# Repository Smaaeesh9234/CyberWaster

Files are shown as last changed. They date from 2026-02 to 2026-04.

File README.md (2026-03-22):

# CyberWaster
Files used for the CyberWaster Project

Place any notes that you have about the cyberwaster here. This should include any hardware and complications

## Lidar System:

$8.00 [Nema 17 Bipolar Stepper Motor](https://www.omc-stepperonline.com/nema-17-bipolar-1-8deg-16ncm-22-6oz-in-1a-3-7v-42x42x20mm-4-wires-17hs08-1004s)

$25.00 [LiDAR sensor](https://www.amazon.com/Wishiot-TF-Luna-Single-Point-Terminal-WiFi_Lora_32/dp/B09PZ559ZB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)

$15.00 (only if doing 360° scan) [Slip ring](https://www.digikey.com/en/products/detail/adafruit-industries-llc/736/5353612)

$7.00 [A4988 Motor Driver](https://www.digikey.com/en/products/detail/adafruit-industries-llc/6109/25897273)

[Arduino Kit Components:](https://www.elegoo.com/blogs/arduino-projects/elegoo-mega-2560-the-most-complete-starter-kit-tutorial)
Arduino Mega

## Motor System

## ROS 2

<tutorial Links here>
https://docs.ros.org/en/humble/Installation.html

## Gazebo

<install and use gazebo links>
https://gazebosim.org/docs/fortress/getstarted/

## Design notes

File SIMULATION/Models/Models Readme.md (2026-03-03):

Place your .stl files here for your models or any other file types. this is for the 3d models specifically

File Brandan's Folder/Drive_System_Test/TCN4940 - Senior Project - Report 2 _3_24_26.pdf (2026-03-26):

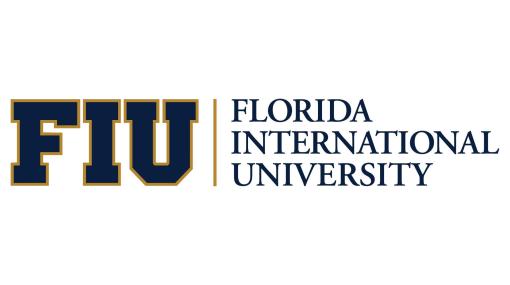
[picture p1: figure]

### Department of Electrical and Computer Engineering

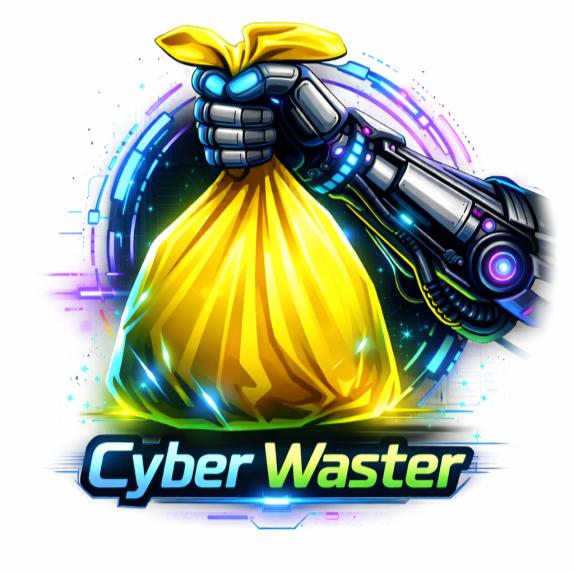
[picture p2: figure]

TCN4940 RVC 1261 - Senior Project Spring 2026

## CyberWaster

### The Waste Handlers

Team Leader: Brandan Gerbers (6448449) Sabrina Ruiz (6338671)
Ellowyn Taylor (6352591)
Samir Zelaya (6474641)
Sebastian Klee (6307554)
Giovanni Nieves (6198045)
Instructor: Gustavo Chaparro Baquero Mentor: Dr. Lauren Ervin

Date: February 2026

## I. SUMMARY AND PROBLEM STATEMENT

Abstract
This project aims to look at how waste collection can be improved by using sensors and automation. Most waste system projects only react to how to solve the problem, instead of using data and trends to make decisions. The current approach is inefficient and labor intensive. We are planning to create a simulated robot environment for testing and use those learnings to create a small-scale prototype that will check the waste level, determine when the bin is full, and navigate to a trash disposal location. This project's primary focus is to create the required technology needed for autonomous navigation and to discover the required sensors for collecting waste level data.

Executive summary

This project approaches waste collection as a logistics and optimization problem by integrating sensing, analytics, and autonomous navigation. The system improves collection efficiency while generating useful insights into waste usage behavior. Designed for scalability, the architecture supports residential, assisted-living, and broader smart infrastructure environments. The system autonomously travels from a designated resting location to a disposal point when waste sensors detect that a bin has reached a predefined fill level. This approach reduces manual effort, improves safety, and demonstrates how automation can enable more efficient and data-informed waste management.

Problem Statement

Current waste collection systems rely on fixed schedules and manual observation rather than real-time data, resulting in inefficient labor usage, increased operational costs, and missed opportunities for optimization. Limited visibility into waste fill levels, weight, and usage patterns prevents waste and recycling services from making informed, data-driven decisions. Routine waste handling presents a physical challenge for individuals with limited mobility, including elderly and physically disabled populations. Tasks such as lifting and transporting waste bins require strength, balance, and repeated effort, which can pose safety risks and reduce independence. As the cost of living continues to rise, inefficiencies in time and labor associated with household waste disposal continue to be a consistent task. These combined challenges highlight the need for a solution that reduces physical effort, improves efficiency, and enables smarter waste management through improved visibility and automation.

## II. NEED SPECIFICATIONS

Objectives | Specification | Justification
1, 6 | An AprilTag signals the robot where to travel. | It automates waste disposal, which would save a person’s time and energy.
2 | LiDAR sensors detect any blocking obstacles in real time and turn accordingly. | It prevents any collisions that could occur and allows the robot to safely navigate in an environment.
3, 4 | An ultrasonic distance sensor alongside 1-4 load cell sensors would measure the levels of waste and signal the robot when it is full. | It ensures that the robot will have accurate detection to correctly decide when traveling is necessary.
5 | The data over time of the waste levels would be analyzed for patterns. | It helps optimize schedules for waste collection and efficiently provides a user’s waste patterns for collectors.

Objectives

1. The robot should be able to carry trash to a designated location.
2. The robot should be able to avoid obstacles in its path.
3. The robot should be able to monitor waste levels.
4. The robot should be able to detect if the trash bin is full.
5. The robot should be able to comprehend data of the user’s waste usage.
6. The robot should be able to reduce the amount of labor for the user.
A. Assumption
⚫ | The QR code sticker is placed correctly at destination points for drop off.
⚫ | Elderly and physically disabled users are willing to allow an assistive robotic system to
| support routine waste handling tasks.
⚫ | Users will not be required to directly interact with the system during normal operation.
⚫ | The LiDAR sensor will detect appropriate sizes of obstacles.
B. Limitation

⚫ | Designed to operate with minimal human feedback
⚫ | Operation is limited to indoor environments and outdoor concrete or similar flat surfaces.
⚫ | The system is not designed to operate on uneven terrain, stairs, or soft ground surfaces
| such as grass or gravel.
⚫ | Performance may be affected by environmental factors such as lighting conditions,
| obstacles, or layout complexity.
C. Operating Environment
Environment Details | Reference Images

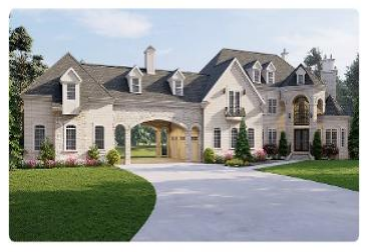
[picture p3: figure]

Residential Single-Family Home
(Large Property)
The system is intended to operate in a residential environment with a paved driveway, landscaped surroundings, and a clearly defined curbside waste collection point. Navigation paths are primarily flat concrete surfaces with minimal elevation changes. Potential obstacles include parked vehicles, outdoor furniture, and pedestrians. Operation is expected to occur in low to moderate traffic conditions.

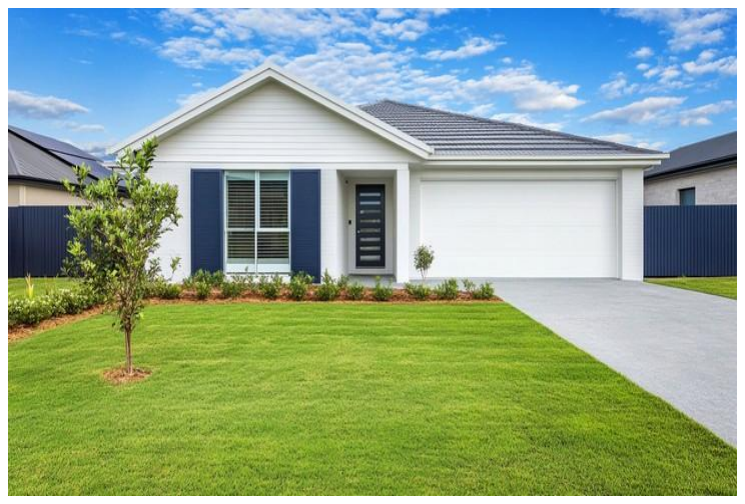
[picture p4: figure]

Residential Single-Family Home (Suburban Property)
This environment represents a typical suburban household with a short driveway and direct access from the home to the curb. The operating surface consists of smooth concrete with grass or landscaping adjacent to travel paths. The system must safely navigate near the home entrance, driveway edges, and curbside collection area while accounting for people, pets, and common household obstacles.

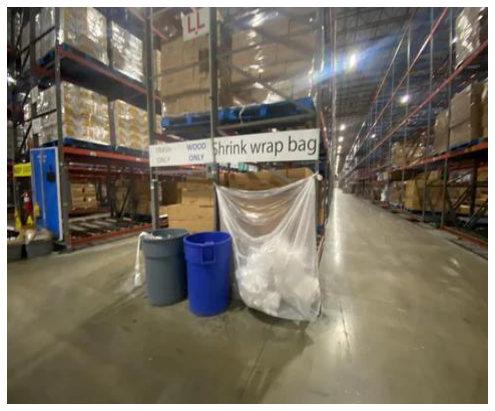
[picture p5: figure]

Indoor Facility / Warehouse-Style Environment This environment represents indoor operational areas such as assisted-living facilities and storage areas. The system operates on polished concrete flooring with defined pathways and frequent human activity. Obstacles may include carts, bins, shelving, and temporary obstructions. Reliable obstacle detection and controlled movement are critical due to shared use of space with staff and occupants.

D. Intended Users and Intended Uses
1. Intended Users:
⚫ | Elderly people (65+)
⚫ | Adults with physical limitations
⚫ | Secondary users such as caregivers and faculty staff
2. Intended Uses:
⚫ | Operates in indoor warehouses or concrete floors.
⚫ | To collect trash and transport it to a drop off location.
⚫ | Reduce labor associated with waste disposal.

## III. NEED ANALYSIS

A. Purpose

The purpose of this project is to address inefficiencies in current waste collection practices by shifting from manual, schedule-based operations to a data-informed, and automated approach. Particular emphasis is placed on supporting populations for whom routine waste handling can be physically challenging, such as elderly and physically disabled individuals. By leveraging sensing, analytics, and autonomous mobility, the project demonstrates how waste monitoring and relocation can be optimized through real-time data and intelligent system behavior.

B. Client Need Statement

The client needs a waste collection system that provides real-time visibility into waste fill levels and usage patterns, reduces dependence on manual observation and fixed schedules, and enables autonomous relocation of waste containers. Smart sensors have helped cities dispatch collection trucks only when needed, reducing unnecessary trips and garbage overflow [1]. The company expressed that it reduced unnecessary collections and garbage overflow. Smart bins can optimize collection schedules by detecting anomalies, such as sudden increases in waste volume [2]. The system should specifically reduce physical effort and safety risks for elderly and physically disabled users while improving overall operational efficiency and decision-making.

C. Data Collection

Needs were identified through:

⚫ | A structured interview with the project mentor acting as the client
⚫ | A survey of potential end users
⚫ | Team brainstorming sessions to uncover additional needs

Mentor-Client Interview

Questions | Answers
On a scale of 1–10, how physically demanding do you find handling waste? | 10
How challenging is this task for you to perform on a regular basis? | Very
How often do you find yourself disposing of waste outside your home? | Once a week
How much assistance would make this task easier for you? | Full autonomy
Would you find analytics about your waste behavior helpful in reducing said waste? | Yes
Is the cost of having waste disposed of something you would like to be reduced? | Yes

Potential End Users Characteristics

Socioeconomics | Age | Primarily elderly adults (65+) and adults with physical limitations; secondary users include caregivers and facility staff.
| Gender | Any
| Income | Expected users would be middle class or higher. This would give an average wage of $56,000+
| Education | Varied educational backgrounds. Systems must be intuitive and not require technical knowledge.
| Disability | Users may have mobility impairments, reduced strength, balance issues, or limited dexterity; the system should minimize physical exertion and risk.
Behavioral | Hobbies | Low to moderate physical activity hobbies. Social hobbies, such as card games with friends and family.
| Reading Interest | General news, lifestyle content, or light informational material. Preference for simple, clear instructions.
| Waste Handling Difficulty | Waste handling may be physically challenging due to weight, bending, balance, or distance to disposal location; users may avoid timely disposal due to effort or safety concerns.
Psychological | Listless | Many expected users would be low energy people, requiring the need for external products to aid in tasks.
| Technology Comfort Level | Varies from low to moderate; the system should feel supportive rather than complex or intimidating.
| Independence | Strong desire to maintain independence and avoid reliance on caregivers.

Team Brainstorming Notes

Identified Challenge | Potential Approach or Consideration
Difficulty moving heavy waste bins | Reduce or eliminate the need for manual bin transport
Risk of falls during waste disposal | Minimize physical handling and walking distance required
Reliance on staff for waste relocation | Enable automated or assisted waste movement
Manual checking of bin fill levels | Provide automated indication of waste capacity status
Desire for resident independence | Support hands-off operation with minimal user interaction
Traffic and obstacle avoidance | High potential of running into people or objects during transit
High potential for missing trash pickup time | A system that is able to transfer waste at a scheduled time or based on environmental condition.
D. Identified Attributes

Main Objective

⚫ Demonstrate relocation systems using simulation and/or a small-scale physical prototype.
⚫ Implement accurate waste capacity sensing to measure bin fill levels.
⚫ Create a simulated environment to demonstrate autonomous robot behavior, system logic, and data flow.
⚫ Collect data to understand the waste usage patterns
⚫ Stay within the project budget

Secondary Objectives

⚫ Define and document a scalable system architecture suitable for expansion to larger environments.
⚫ Design and implement a small-scale physical prototype to validate real-world feasibility.
⚫ Trigger collection and relocation behavior based on predefined waste thresholds. ⚫ Checking the bin weight to prevent overloading the robot with waste

⚫ Limit the movement of the robot if the load is too heavy

Constraints

⚫ Total prototype system cost shall not exceed $800
⚫ Robot shall safely carry a minimum payload of 5 pounds
⚫ Robot shall autonomously navigate to a designated location 15 feet away with a positional accuracy of ±1 foot
⚫ System shall operate reliably on cement flooring and be able to have obstacle detection
⚫ Power system shall support at least two complete autonomous relocation cycle per charge
E. Grouped Objectives

The remaining objectives were grouped into parent categories to clarify design priorities.

Safety

⚫ | The system should operate without posing risk to users
⚫ | The system should operate without posing risk to pets or local wildlife
⚫ | All electrical and battery parts should be protected to prevent any shocks or fire from
| happening.

Usability

⚫ | The system should be easy to operate and understand
⚫ | Optional commands to enhance the user experience and improve the product as the
| user becomes familiar with it
⚫ | The system should provide some feedback to the user about the waste level.

Reliability

⚫ | The system should function consistently with minimal intervention
⚫ | The system should move smoothly and avoid any obstacles in its path.
⚫ | The system should be able to handle different terrains without getting stuck.
F. Resulting Problem Statement

This project aims to design an autonomous waste monitoring and relocation system that addresses inefficiencies in manual waste handling while improving safety, usability, and reliability. The system should reduce physical effort and safety risks for users with limited mobility, support independent operation, and provide consistent, data-informed waste handling behavior in residential and assisted-living environments.

The objectives identified through this need specific and analysis provide the foundation for defining the specifications and requirements to ensure the project solves a real-world problem.

## IV. FEASIBILITY AND RISK ANALYSIS

A. Technical Feasibility

CyberWaster relies on established robotics, such as the load cells, LiDAR sensors, or the AprilTags. These components are available and can be obtained locally or through online purchases. The system will be using already established frameworks like ROS 2 and Gazebo for simulation. This project relies on existing technologies, making the overall technical risk moderate but manageable.

Below is an assessment conducted by the team ranking the feasibility of set attributes. 5 is a highly feasible option, and 1 is a low-chance feasibility.

Attribute | Score | Why | Solution
Does the technology exist? | 5 | Yes. | Using existing components like LiDAR sensors, wheels, Gazebo simulation, etc.
Is it available locally or online? | 5 | Yes, both. | All components are distributed in stores and online stores like Amazon. Some members possess a 3D printer, and FIU has several as well.
Can it be obtained? | 4 | Yes, however, we require finance. | Our team set price targets for hardware, funding the project ourselves by using open-source software packages.
Are fundamentally new inventions required? | 4 | Just the 3D structure of CyberWaster. | Design and print the 3D structure of CyberWaster.
How much Technical Risk is there? | 3 | Ensuring functionality of the hardware and software can be difficult. | Completely build CyberWaster and test its function in different layouts with the simulation.
Total | 21
Average | 4.2

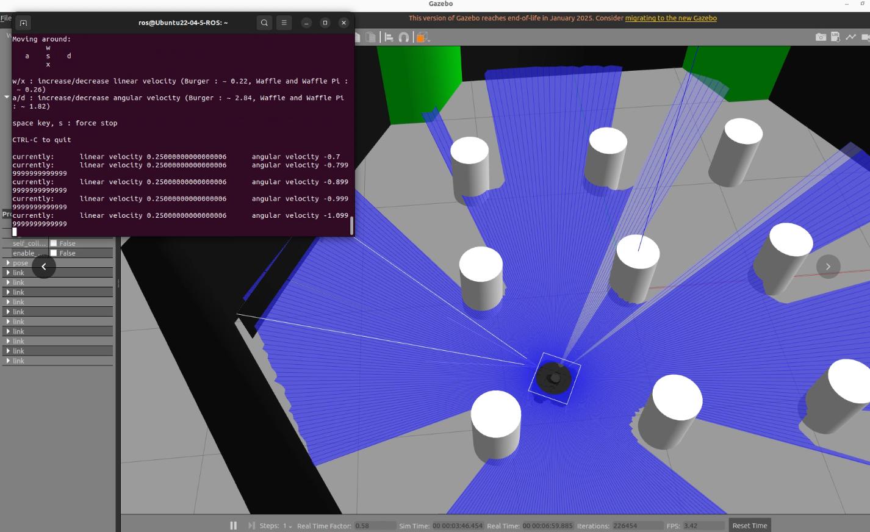
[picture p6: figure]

Figure 1: Early Testing with ROS2 + Gazebo during Turtle3 tutorial using lidar on mobile robot

B. Resource Feasibility

Our team has sufficient skills to complete the project; however, there are still some new technologies that are new to us. Some of us have experience in software and hardware development, which assists us in building CyberWaster and creating its simulation in Gazebo. There are still some things we are learning like integrating ROS 2 in this project. Despite the challenges, we are making progress in completing the project, thus making the overall resource risk moderate.

Attribute | Score | Why | Solution
Do we have sufficient skills? | 4 | ROS2 and Gazebo simulation are new to us. | Our mentor provided some tutorial links, and we are also practicing it as a team.
Do we have sufficient equipment? | 5 | Yes, we acquired all the components as needed. | Keep components managed during development and testing.
Do we have a sufficient number of people? | 5 | Yes, 6 members is enough. | The workload will not be too extensive.
How much Resource Risk is there? | 4 | If any component breaks, it will delay progress due to shipping. | Be careful and treat our hardware components with care.
Total | 18
Average | 4.5

C. Economic Feasibility

This project’s system must have a budget to be realistic for a senior project. The required components used in CyberWaster are affordable, such as the wheels, sensors, etc. Additionally, its body is 3D printed, which significantly reduces manufacturing costs. We decided on using simple solutions like using magnets to hold a specific section of the robot together. Since most of the components are not excessively expensive and most of its structure is built through 3D printing, its overall economic risk is low.

Attribute | Score | Why | Solution
Is the project possible, given budget constraints? | 5 | Most of the components needed, like wheels, sensors, and other electronics, are affordable. | Continue as planned to select cost efficient components.
Do the design choices reduce the overall cost of the project? | 5 | CyberWaster’s body is primarily made of 3D-printed material, significantly reducing manufacturing costs. | Construct the structure from 3D-printed materials to reduce costs.
How much Economic Risk is there? | 4 | Some components possibly could be damaged during assembly and testing. There is a risk of electric shock. | Handle each component carefully and plan for replacements if needed. Maintain low voltages of less than 24V.
Total | 14
Average | 4.7
D. Schedule Feasibility

We had discussions and decided to assign tasks to each member to keep our pacing organized and efficient for this project. We considered the distinct categories such as the development of Gazebo simulation, hardware integration, software inclusion, and eventually system testing. Even though we will face challenges that may hinder our progress, we believe that fulfilling our assigned tasks will improve our chances of meeting our milestones for the Preliminary Design Review and Critical Design Review. Thus, our overall schedule risk will be considered moderate when considering the complexity of completing CyberWaster.

Attribute | Score | Why | Solution
What are the chances of meeting the immediate mileposts? | 4 | Our team divided tasks amongst each other to keep organization and progress consistent. | Resume the ordered assignments and track progress with each member.

What are the chances of meeting the PDR (Preliminary Design Review) requirements? | 4 | Milestones such as the simulation environment and the construction of CyberWaster have been fulfilled. | Keep progressing through the hardware and software integration before the deadline.
What are the chances of meeting the CDR (Critical Design Review) requirements? | 3 | Some essential features like ROS2 and sensor navigation are still being implemented and may require more testing. | Continue researching ROS2 integration and start testing CyberWaster before the deadline.
Total | 11
Average | 3.7
E. Cultural Feasibility

CyberWaster’s purpose is to assist others and make the disposal process more efficient. By reducing the physical effort required to remove waste, our project helps reduce labor and improves the safety of people who struggle with lifting or transporting trash, like elderly people. Assistive technologies have already been implemented to help elderly people in different aspects such as telehealth services, wearable devices, smart home systems, assistive robots, etc. [10] So, the cultural risk is considered low because of how widely assistive technology has become to society.

Attribute | Score | Why | Solution
Will there be a positive impact on the local culture? | 5 | CyberWaster helps reduce the physical effort that is needed to dispose of waste for those who struggle with it. | Ensure that the design of the system is fulfilled to support accessibility.
Will there be a positive impact on global culture? | 5 | Assistive technologies are used to support people and improve the quality of life. | Explore methods on how automation helps people with daily tasks.
Will there be potential labor objections to this system? | 5 | This system intends to help others instead of replacing workers. | Clarify the purpose of assistive technology and this project’s goal.
How much Cultural Risk is there? | 5 | Assistive technologies are accepted worldwide in society. | Ensure that the audience knows how CyberWaster benefits them.
Total | 20
Average | 5

F. Legal Feasibility

This project does not present any significant legal risks as it is being developed as an academic prototype for demonstration purposes. However, when considering our CyberWaster, it will be made of commonly used components that many other service robots use. This ensures that its hardware tools would not just malfunction and explode compared to making a
component from scratch. Additionally, our robot is intended to operate in a controlled environment, limiting potential liability concerns. It has been researched that service robots used in social environments may raise legal frameworks like safety; however, existing frameworks can address these issues as technology develops more. [11] Overall, the legal risk is determined to be low due to following basic safety considerations and using standard technology.
Attribute | Score | Why | Solution
Are there organizational conflicts or policies that could affect this project? | 5 | This project is an academic prototype for demonstration purposes and follows FIU guidelines. | Ensure that the design of the system is fulfilled to support accessibility.
Are there any laws or regulations that could impede the project? | 5 | All components are the same components that are available in other service robots and do not consist of restricted technologies. | Explore methods on how automation helps people with daily tasks.
Are there any laws or regulations that could limit the project? | 4 | CyberWaster is meant to operate in controlled environments, reducing limitations. | Clarify the purpose of assistive technology and this project’s goal.
How much Legal Risk is there? | 5 | Our project follows the same current legal frameworks of service robots that focus on safety and liability. | Ensure that all safety standards are followed and do responsible testing practices.
Total | 19
Average | 4.8
G. Marketing Feasibility

Our mobile robot addresses the practical problem of waste disposal for people who struggle doing the labor and elderly people. It can be physically demanding to lift trash and put it away. Since assistive technology is more common in current times, having the ability to have a mobile robot to handle your waste seems plausible for the audience. This project has the potential to be applicable in residential homes or facilities that may need it. The overall marketing risk is low because of the solution to help people in trash disposal and our world’s growing trend in

technology.

Attribute | Score | Why | Solution
Will the target audience benefit from CyberWaster? | 5 | The robot aids people who have difficulty disposing trash, especially elderly and disabled persons. | Complete the system’s design to support accessibility and ease of use.
Is there a necessity for a system that assists with waste disposal? | 4 | Disposing waste can be physically demanding, and service robots can help people perform their daily tasks. | Keep developing the system to solve challenges in waste disposal.
How much Marketing Risk is there? | 4 | Our system solves a real-world problem and aligns in the growing trend of assistive technology through automation. | Demonstrate the benefits of our project through testing and its final showcase.
Total | 13
Average | 4.3
H. Risk Assessment

A risk analysis is essential for identifying potential challenges that could affect our project of CyberWaster’s success. By evaluating risks early, our team can take steps to manage and reduce their impact.
- Technical
♦ | T.1: Difficulties with ROS2 integration between hardware and software.
♦ | T.2: Inaccurate sensors when detecting obstacles or level of waste.
♦ | T.3: Navigation issues when moving to its destination point.
♦ | T.4: Motor and Drive Calculations and selection to ft requirements of system
- Resource
♦ | R.1: The team’s learning curve with ROS2, Gazebo simulation, and robotics.
♦ | R.2: Delays if a hardware component breaks during development.
- Economic
♦ | E.1: Unfortunate extra costs if components become damaged during
| development.
- Schedule
♦ | S.1: Delays during ROS2 integration with CyberWaster and Gazebo simulation.
♦ | S.2: Time conflicts between project work and other responsibilities.
- Cultural
♦ C.1: Users could be hesitant to entrust a robot with their daily tasks.
- Legal
♦ L.1: Possible safety concerns if the robot were to malfunction during operation.

- Marketing
♦ | M.1 Skepticism from users about the system’s benefits.
| Likelihood of Occurrence
Very Likely | Possible | Unlikely
Undesirable Outcomes | Class IV
| Class III | T1, S1 | T2, T3
| Class II | | R1, R2, S2, C1 | E1, L1, M1
| Class I
Risks | T1, T2, T3 | R1 | R2, E1 | S1, S2 | C1, M1 | L1
Actions | Continue with the project’s testing and development. | Learn and practice ROS2 and Gazebo. | Handle all components with care. | Assign tasks and ensure time management is good. | Showcase the benefits of the system. | Ensure operations are safe.

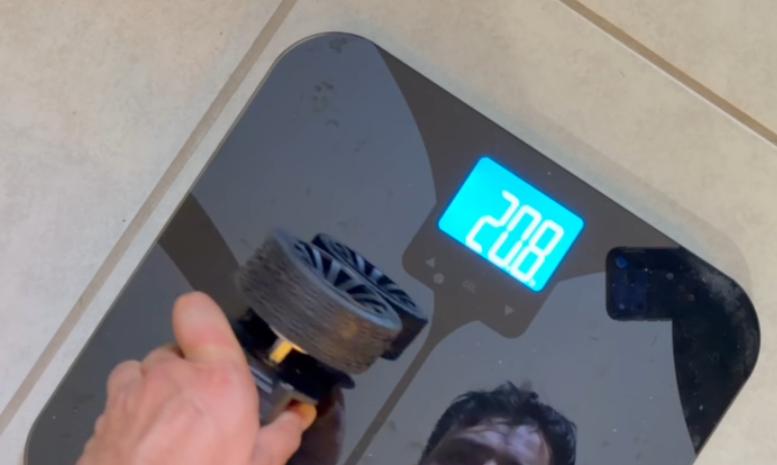
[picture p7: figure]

Figure 2: During Testing Confirming Wheel Motion with excess load applied via scale

## V. Patents & Intellectual Property

A patent, by definition [22], allows inventors to protect their inventions. They give an inventor the right to exclude others from making, using, selling, or offering the invention for sale, and from importing the invention into the United States for a limited time, and to others if they decide to. It is worth mentioning Patent rights, which are claimed by patents that protect the invention as claimed.

Copyright is the product of the media itself. So, it protects original works of authorship, such as books, music, and films, giving creators exclusive rights to reproduce and distribute their work. Copyright is usually secure from the moment it is created. However, registration is not a condition of copyright protection.

Trademarks are any word, phrase, symbol, design, or combination used to identify the source of goods or services and distinguish them from other sources or products like it. They help people identify the said machine or device in question. While secure and mostly the same, except that it identifies and distinguishes the source of a service rather than a product in question.

There are also trade secrets, which are parts that contain confidential information and features that set them apart from similar products on the market.

Now I’m sure you’re asking two questions. How does one go about making a patent, and why is it so important to our project? Well, a patent, like all things, has a process. First, we need to describe what makes our creation unique. What it innovates and so forth. Secondly, the United States Patent and Trademark Office (USPTO) require one to disclose any publication, patent, or other written document that you know to be relevant to your patent. Thus, it is important to decide on the kind of protection of your creation you want (parts, specifics, etc.), which is the third step, and how flexible or inflexible the rules of what you lay down as your copyrighted material can be improved on a later date, or if it's done now, strictly. After which, all you have to do is submit it to the (USPTO) United States Patent and Trademark Office and wait. If it gets approved, you’re all done. [23]

As for why it’s so important to cyberwaster, having a patent allows it to be global, preventing it from being stolen and sold without permission. It gives us the ability to go ‘global’ with our robot. Not having a patent means anyone can manufacture and sell the product without giving credit or permission. [24]

As for specifics on which patents are suitable for robots, we found and provided two examples. The first one has basically its assembly copyrighted. Along with specifics on the said parts. Being a robotic arm that must be done in a certain way, even down to its color, since that was its finalized and global design. It does have some flexibility [25]. The second example has a magnetic material itself, along with the circuit board in question, protected by a patent. In fact, most of it is in such detail that one can’t even replicate or rip it off in the slightest, which is how a patent protects the invention. [26]

## VI. Theory Model Analysis of Potential Ethical Dilemmas of the Project

Theory Model analysis is a step-by-step process of following a particular framework to check on the ethicality of a project. This paper will be using the PLUS framework to break down the CyberWaster project into manageable pieces that will cover any problems that may arise from this project. PLUS is an acronym that means:

- Policies.
- Does this project follow consistent policies and procedures?

Our project needs to have the creation of policies during development as our ‘company’ that is running the project did not exist before the development of this project. As such, our policies are liable to change:

à We are obliged to protect animals and humans, and to help the users of our product for the sake of betterment in their lives.
à The user will remain in control of the CyberWaster’s functionality, serving a supportive role.
à The decision-making process the CyberWaster makes will be made clear to users to ensure understanding.
- Legal.
- Is it acceptable under applicable laws and regulations?
The Cyberwaster follows known laws and regulations of Miami-Dade County.
This includes but is not limited to:
1. Leak-proof Design
The CyberWaster uses a solid design which will not have any leaks during regular use. Our trash can be replaced with little effort or cost since our system is modular. The ability to get a new can and attach it to our CyberWaster will be simple.
The reason this replacement may be needed is in the case of the trashcan breaking or falling into disrepair.
2. Weight Limit
The weight of waste in combination with the bin must be less than 50 pounds Current plans for the CyberWaster are limited to a weight of 30 pounds, with a capacity to hold 15 pounds. Current development predicts that the weight of the CyberWaster will be significantly below this range, keeping the overall weight well below 50 pounds.
3. Outdoor Environment
The CyberWaster is designed to go back inside promptly after it has been emptied, causing it to easily fulfill this law at a higher degree than normal bins used.
- Universal.
- Does it comply with the universal principles and values of our organization? It is inherited that the CyberWaster will share the principles of our organization. This is since the organization was formed alongside the CyberWaster. The policies of our organization are formed alongside the CyberWaster. Our top goals are to help humanity by helping those who are not fully able-bodied.
- Self.
- Does it fulfill our definition of right and good?

Our CyberWaster product follows strict guidelines for the express purpose of helping people. This aligns with our ethical guidelines to help people who are not able-bodied. This product can also help people who are fully able, which gives us an extra incentive to create our product.

## VII. Health and Safety

When we are creating a robot, we all think about the health and safety of the users who will be using our robot. A safe robot is designed to not hurt anyone, avoid any obstacle it sees, and have its wire covered so that our user doesn’t get burned or shocked. Then there is an unsafe robot where it can harm the users or the environment they are in. For example, it might have exposed wires on them, overheat while working in the sun, or moving unpredictably and break items as it is working. I should mention that our prototype will have its wire showing while we are building and testing it, but the final project will have its wires covered so that the user won’t get shocked. Since we are making our robot for elderly people and adults with physical limitations.

Our main goal is to make it easy for our users to avoid getting injured while taking out the trash. We also have a main safety goal which is to reduce the chance of harming our users, their pets, and the environment. Which is why we are planning our robot to slow down or completely stop if it senses an obstacle in its path so that it doesn’t hurt anyone. Like for example, they could get back pain from carrying heavy waste or trips on the waste or the bin. We want our robot to help make it easier for our users to handle waste. Our plan with our robot is to help our users by trying to avoid back pains, slips, and even overdoing them. We want to have all the electrical parts for the robot covered because we don’t want the user to get shocked while touching the robot. We want to either make labels or cover some parts of the robot so that our users won’t get burned to see how hot the material can get while it is in the sun or while it is running.

We are planning to add sensors to our robot so it can detect any obstacles and avoid anything as the robot is taking out the trash. The sensor would help the robot avoid pets, the user itself, and their belongings. Our robot is going to be used outside on a flat surface because if you use it on stairs, grass, or uneven surface the robot wouldn’t work properly or damage. This is why we were thinking of creating instructions to have our robot understand the robot limitations and how to use it safely. We also ensure that our robot is made from safe materials, as some people make robots with toxic components that could harm our users. Which is why we want to avoid using that material and ensure users' safety while operating our robots. We hope that our robot will help users handle waste more easily without putting themselves in danger.

As mentioned before, my team wants to ensure our robot is made from safe materials because some of the parts we use can be harmful to our users. We found a research paper called “Ethical considerations in the use of social robots for supporting mental health and wellbeing in older adults in long-term care.” [3] This research paper talks about how some robots are made from toxic materials that can be dangerous if anyone touches or inhales it over a long time. This made us realize we need to carefully choose the materials we use, so we don’t expose our users to illness or health problems later. Since we plan to build our robot using 3D printing, we thought it best to research the associated risks. We found an article called “The

Health Effects of 3D Printing” [5] that explains that the common 3D printing material, ABS, releases tiny, harmful chemicals that, when heated, can irritate our lungs and cause health problems later. While PLA is the safer option to use because it produces fewer chemicals into the air. Based on two sources, we need to choose carefully on which material we are going to use because we want our robot to be safe to use and not harm anyone who uses it.

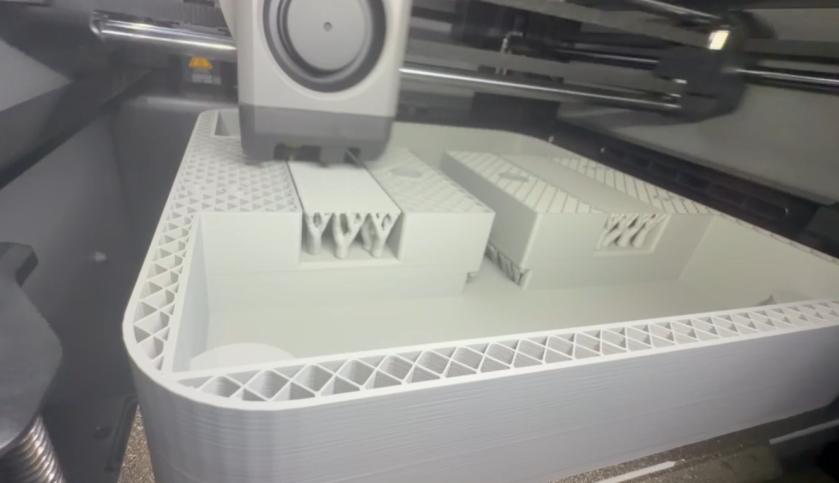
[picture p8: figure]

Figure 3: Photo take during 3D printing of our prototype CyberWaster

Materials | Safe to Use | Risk if Uses
Plastic | Need to choose a non-toxic plastic that doesn’t release chemicals when heated. | All plastics will release harmful chemicals when its heated it up that will cause irritation on the lunges
3D Printing | Maybe PLA because it produces less harmful chemicals in the air. | ABS produces a lot of styrene and tiny particles that will irritate your lungs and cause health problems.

As we discussed before, we don’t want our robot to hurt anyone, which is why we use sensors to avoid obstacles and cover its wires, so users won’t get shocked or burned. We found another research paper called “Robotics to Enable Older Adults to Remain Living at Home”, which talks about how robots are helping older adults to stay safe at home by helping them avoid falling and moving around easily. [4] It does mention how it helps monitor its environment and reminds people to take care of themselves, like a service dog. This paper helps us better understand how we want to make our robot, because we need it to notice its surroundings so it can know where the trash is and whether there are any pets around. Also, it helps us understand more on how to make our user safe as we are making the robot. To show how our robot is making the decision while moving, we created a flowchart below.

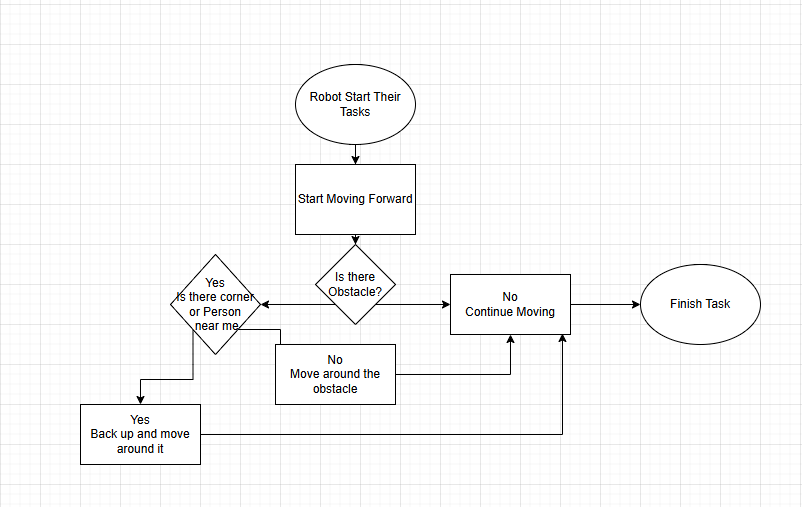
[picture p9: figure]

Figure 4: This flowchart shows how the robot is deciding what to do when it senses something in its path.

IP (Ingress Protection) [21] ratings are a standardized classification system used to define the level of protection an enclosure provides against the intrusion of solid particles (such as dust) and liquids (such as water). This is highly relevant to the CyberWaster system, as the device may operate both indoors and outdoors, exposing it to environmental contaminants. During operation, particularly when waste is transported, dust and debris may be disturbed, requiring adequate sealing to protect internal electronics and mechanical components. Additionally, operation in potentially damp or wet environments introduces risk to electrical systems, making moisture protection critical.

From a design and compliance perspective, selecting an appropriate IP rating supports reliability, safety, and regulatory alignment, including potential insurance and consumer safety requirements. An IP67 rating is a strong candidate for this application, as it ensures complete protection against dust ingress and provides resistance to temporary immersion in water. This level of protection enables the system to function safely in outdoor conditions such as rain exposure while maintaining the integrity of internal components.

Overall, we want our robot to keep the users safe and healthy while taking out the trash easier for them. We just want to make sure that the wires are covered; we are using non-toxic materials that won’t affect the elderly and people with physical limitations later in life and prevent any shock or burn when touching our robot. Also, we need to make sure that our robot knows its surroundings before moving around because we don’t want the robot to hit anything or anyone as it is running. Our focus on our project is to have our robot help with waste without causing any issues to our users and feel safe around it.

## VIII. Sustainability and Standards

Compliance with established robotics and machinery safety standards is a critical aspect of the system design, particularly due to the presence of autonomous motion and operation in environments where humans or obstacles may be present. One of the primary standards considered is ISO 10218 [7] which defines safety requirements for industrial robots and robotic systems. While the system is not a traditional fixed industrial manipulator, meaning a stationary robot arm mounted in one location, the core safety principles outlined in this standard are still applicable due to the use of motors, sensors, and autonomous control. We believe these principles remain highly relevant, especially since the system presents similar risks related to motion, actuation, and interaction with its environment. These ideas also align with broader research in mobile robotics where safe navigation and predictable system behavior are necessary for operation in real-world environments.

A key requirement defined in ISO 10218 [7] is risk assessment and hazard identification, in order to align with this, the system could be designed with consideration of potential failure conditions such as unintended motor activation, communication failure between control components, sensor inaccuracies, and possible collisions. These risks can be addressed through the use of the Robot Operating System (ROS), which allows for modular communication between system components and supports continuous monitoring of sensor inputs and control signals. For example, sensor data from LiDAR and ultrasonic modules could be continuously verified, and any weird readings might trigger a system response such as stopping or adjusting movement. We think incorporating this type of monitoring is important for maintaining safe operation, particularly in environments that may be unpredictable.

Another important requirement outlined in ISO 10218 [7] is safe motion control. The standard in this case emphasizes limiting speed, acceleration, and overall system behavior to reduce the likelihood of injury or damage. To reflect this, the drive system would incorporate defined limits on motor output with motors being controlled using PWM and potentially feedback-based control to maintain predictable movement. Within ROS, motion commands are regulated through global and local planners. The local planner continuously generates collision-free trajectories and adjusts velocity commands using real-time feedback, resulting in smooth and stable motion rather than abrupt transitions. This is especially important for a mobile platform operating near obstacles or people. [29] These algorithms often come in a format that will append extra path onto the given path instead of needing to start a new path or recalculate the path for any found obstacles [27].

Continuing on, the standard also highlights the importance of protective measures and safeguarding. In fixed industrial systems, this is often achieved through physical barriers, but for a mobile platform, safety relies more on sensor-based detection. LiDAR would be used in our case as the primary sensing method to continuously scan the environment and detect obstacles in real time. This data can then be processed within ROS to generate maps and determine safe navigation paths. Ultrasonic sensors could also serve as an additional layer of detection for close-range obstacles, providing redundancy in case of LiDAR limitations.

Emergency stop functionality is another requirement emphasized in ISO 10218 [7] so to address this, both hardware and software-based stop mechanisms could be incorporated. A physical kill switch could disconnect power to the motors while a software-based stop command within ROS might override active processes and bring the system to a controlled stop.

In addition to ISO 10218, ISO 12100 [8] provides general guidelines for machine safety, particularly in the areas of risk assessment and risk reduction. This standard supports the idea that hazards should be minimized at the design stage rather than addressed later. For example, limiting motor torque and maximum speed could reduce the severity of potential impacts, while thoughtful placement of components may help reduce mechanical or electrical risks.

## References

[1] New York Post, “Self-driving bins, noiseless EV garbage trucks are future of trash collection,” New York Post, Aug. 28, 2025. [Online]. Available: https://nypost.com/2025/08/28/business/self-driving-bins-noiseless-ev-garbage-trucks-are-future-of-trash-collection/. (https://nypost.com/2025/08/28/business/self-driving-bins-noiseless-ev-garbage-trucks-are-future-of-trash-collection/) Accessed: Feb. 11, 2026.
[2] The Conversation, “From robotic trucks to smart bins: How technology is helping cities sort their waste problem,” The Conversation, 2025. [Online]. Available: https://theconversation.com/from-robotic-trucks-to-smart-bins-how-technology-is-helping-citiessort-their-waste-problem-260023. (https://theconversation.com/from-robotic-trucks-to-smart-bins-how-technology-is-helping-cities-sort-their-waste-problem-260023) Accessed: Feb. 11, 2026.
[3] Frontiers, “Ethical considerations in the use of social robots for supporting mental health and wellbeing in older adults in long-term care,” Frontiers. 31, March 2025. [Online] Link: https://pmc.ncbi.nlm.nih.gov/articles/PMC11994439/pdf/frobt-12-1560214.pdf
[4] Hindawi Publishing Corporation, “Robotics to Enable Older Adults to Remain Living at Home,” Journal of Aging Research. 1, October 2012. [Online] Link: https://pmc.ncbi.nlm.nih.gov/articles/PMC3529482/pdf/JAR2012-538169.pdf
[5] American Libraries, “The Health Effects of 3D Printing,” American Libraries. 11, October 2016. [Online] https://americanlibrariesmagazine.org/2016/10/11/the-health-effects-of-3dprinting/ (https://americanlibrariesmagazine.org/2016/10/11/the-health-effects-of-3d-printing/)
[6] T. Kiser, “E.T.H.I.C.S. - A simple yet powerful acronym to anchor workplace values,” LinkedIn, https://www.linkedin.com/pulse/ethics-simple-yet-powerful-acronym-anchorworkplace-tom-kiser-gtujc/ (https://www.linkedin.com/pulse/ethics-simple-yet-powerful-acronym-anchor-workplace-tom-kiser-gtujc/) (accessed Mar. 14, 2026).
[7] International Organization for Standardization, “ISO 10218-1:2011 – Robots and robotic devices — Safety requirements for industrial robots.” https://www.iso.org/obp/ui/en/#iso:std:iso:10218:-1:ed-3:v1:en. Accessed: Mar. 16, 2026.
[8] International Organization for Standardization, “ISO 12100:2010 – Safety of machinery — General principles for design — Risk assessment and risk reduction.” https://www.iso.org/obp/ui/#iso:std:iso:12100:ed-1:v1:en. Accessed: Mar. 16, 2026.
[9] D. Trejo, N. Biedma, D. López De Luise, L. Rancez, G. Barrera, and L. Isoba, “Performance Evaluation for Autonomous Mobile Robots,” Proceedings of the 5th International Conference on Agents and Artificial Intelligence (ICAART), 2013. https://scispace.com/pdf/performanceevaluation-of-autonomous-mobile-robots-4zdkh20ti0.pdf. (https://scispace.com/pdf/performance-evaluation-of-autonomous-mobile-robots-4zdkh20ti0.pdf) Accessed: Mar. 16, 2026.
[10] M. N. Albarqi, “Exploring the Effectiveness of Technology-Assisted Interventions for Promoting Independence in Elderly Patients: A Systematic Review,” Healthcare, vol. 12, no. 21, pp. 2105–2105, Oct. 2024, doi: https://doi.org/10.3390/healthcare12212105. Accessed: Mar. 16, 2026
[11] T. Dreier and I. Spiecker genannt Döhmann, “Legal aspects of service robotics,” Poiesis & Praxis, vol. 9, no. 3–4, pp. 201–217, Nov. 2012, doi: https://doi.org/10.1007/s10202-012-0115-4.
[12] “Company ethics policy explained: Components & Best Practices,” Company Ethics Policy Explained: Components & Best Practices, https://www.faceup.com/en/blog/companyethics-policy (https://www.faceup.com/en/blog/company-ethics-policy) (accessed Mar. 16, 2026).
[13] “Ethical implications of AI in waste systems. → scenario,” Prism, https://prism.sustainabilitydirectory.com/scenario/ethical-implications-of-ai-in-waste-systems/ (https://prism.sustainability-directory.com/scenario/ethical-implications-of-ai-in-waste-systems/) (accessed Mar. 16, 2026).
[14] S. Langman, N. Capicotto, Y. Maddahi, and K. Zareinia, “Roboethics principles and policies in Europe and North America,” SN applied sciences, https://pmc.ncbi.nlm.nih.gov/articles/PMC8572833/#:~:text=A%20robot%20may%20not%20injure,not%20applicable%20to%20robotics%20today. (accessed Mar. 16, 2026).
[15] “Residential garbage,” City of Miami Beach, https://www.miamibeachfl.gov/city-hall/publicworks/sanitation-division/residentialgarbage/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,th an%2024%20hours%20prior%20to%20pick%20up (accessed Mar. 16, 2026).
[16] “Company ethics policy explained: Components & Best Practices,” Company Ethics Policy Explained: Components & Best Practices, https://www.faceup.com/en/blog/companyethics-policy (https://www.faceup.com/en/blog/company-ethics-policy) (accessed Mar. 16, 2026).
[17] P. Steven Mintz, “A new approach to teaching ethical decision making to accounting students,” The CPA Journal, https://www.cpajournal.com/2019/10/14/a-new-approach-toteaching-ethical-decision-making-to-accountingstudents/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,of%20the%20decision%20at %20hand. (accessed Mar. 15, 2026).
[18] “Ethical implications of AI in waste systems. → scenario,” Prism, https://prism.sustainabilitydirectory.com/scenario/ethical-implications-of-ai-in-waste-systems/ (https://prism.sustainability-directory.com/scenario/ethical-implications-of-ai-in-waste-systems/) (accessed Mar. 14, 2026).
[19] T. Kiser, “E.T.H.I.C.S. - A simple yet powerful acronym to anchor workplace values,” LinkedIn, https://www.linkedin.com/pulse/ethics-simple-yet-powerful-acronym-anchorworkplace-tom-kiser-gtujc/ (https://www.linkedin.com/pulse/ethics-simple-yet-powerful-acronym-anchor-workplace-tom-kiser-gtujc/) (accessed Mar. 14, 2026).
[20] “The ethics of waste: Examining our responsibility to the planet,” Home, https://www.vanellagroupmn.com/the-ethics-of-waste-examining-our-responsibility-to-theplanet (https://www.vanellagroupmn.com/the-ethics-of-waste-examining-our-responsibility-to-the-planet) (accessed Mar. 16, 2026).

[21] “IP Code,” Wikipedia, The Free Encyclopedia. [Online]. Available: https://en.wikipedia.org/wiki/IP_code. [Accessed: Mar. 18, 2026].
[22] “Explore intellectual property,” USPTO, https://www.uspto.gov/kids/explore-intellectualproperty (accessed Mar. 14, 2026).
[23] Esq. Joe Runge, “How to get a patent in 5 steps,” LegalZoom, https://www.legalzoom.com/articles/how-to-get-a-patent-in-5-steps (accessed Mar. 19, 2026).
[24] B. Tran, “Answer for what is the benefit of having a patent?,” PatentPC, https://patentpc.com/blog/what-is-the-benefit-of-having-a-patent (accessed Mar. 19, 2026).
[25] “US8322249B2 - Robot Arm Assembly,” Google Patents, https://patents.google.com/patent/US8322249 (accessed Mar. 14, 2026).
[26] “Cleaning robot,” USPTO.report, https://uspto.report/patent/grant/10,994,918 (accessed Mar. 14, 2026).
[27] YouTube, https://www.youtube.com/watch?v=uls-WmxRiTw (accessed Mar. 14, 2026).
[28] “Ai, deep learning and robotics,” ROS2: Path Planning Algorithms Python Implementation, https://robotics.snowcron.com/robotics_ros2/multi_bot_nav_03_intro.htm (accessed Mar. 14, 2026).
[29] “ROS Navigation Stack Explained: Guiding Your Robot to its Destination,” AURA Digital Labs, https://www.auradigitallabs.com/blog/posts/ros-navigation-stack-explained (accessed Mar. 24, 2026).

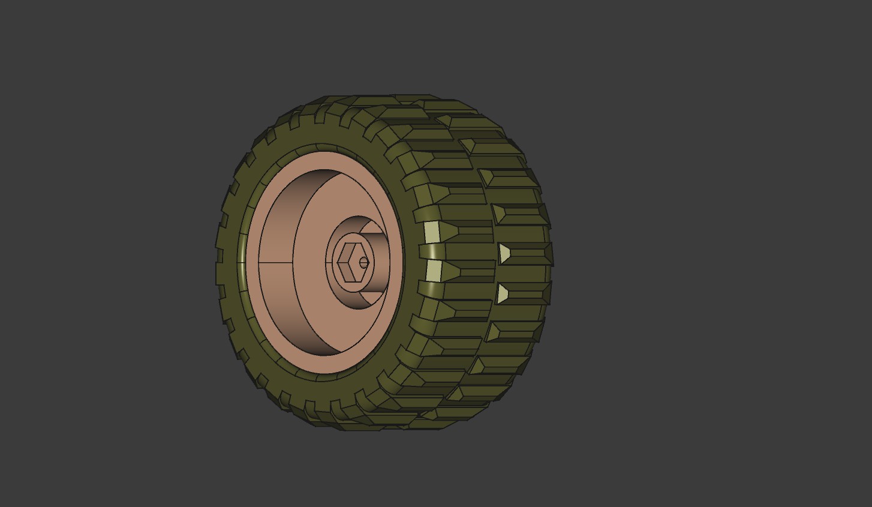
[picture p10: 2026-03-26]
Brandan's Folder/Drive_System_Test/Hardware/rc-wheel-85-mm-1.snapshot.1/Wheel 2 85 mm.jpg

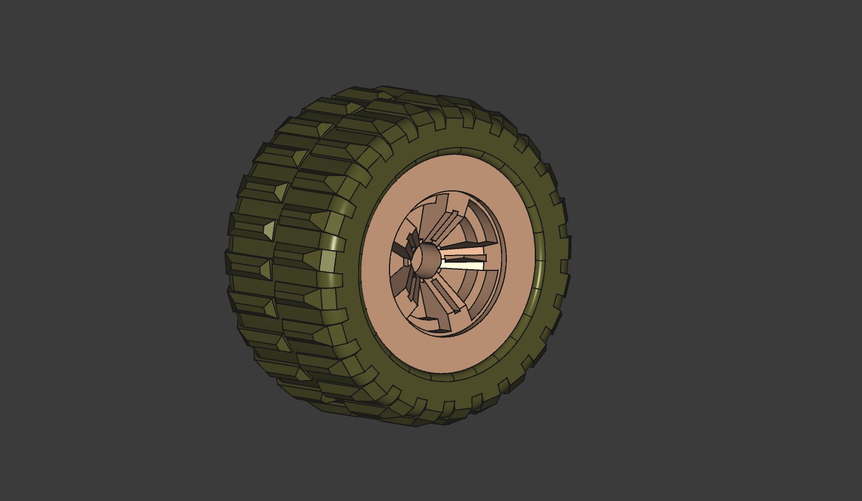
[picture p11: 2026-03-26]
Brandan's Folder/Drive_System_Test/Hardware/rc-wheel-85-mm-1.snapshot.1/Wheel 85 mm.jpg

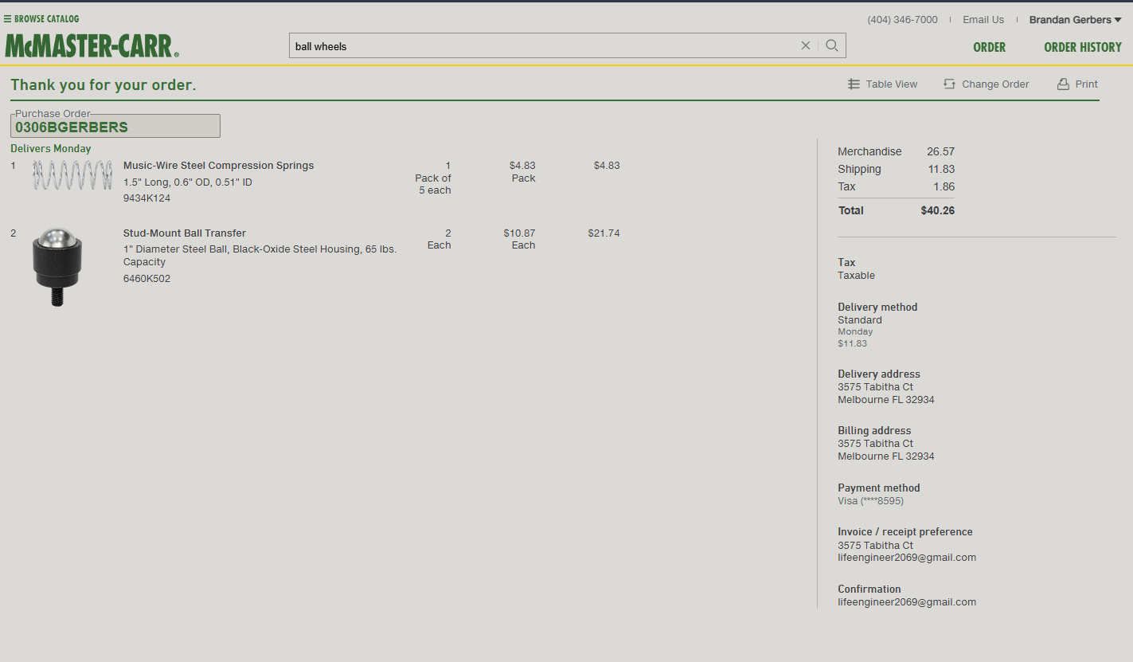
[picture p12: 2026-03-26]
Brandan's Folder/Drive_System_Test/Hardware/Springs/Screenshot 2026-03-06 215601.png

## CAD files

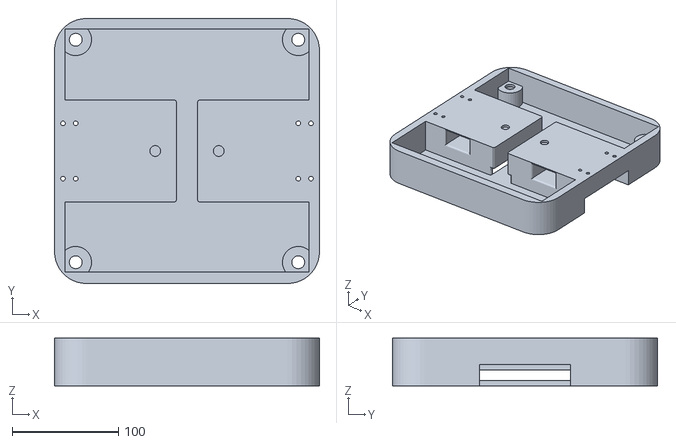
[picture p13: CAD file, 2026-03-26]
Brandan's Folder/Drive_System_Test/3DPrints/Frame_03_06_26.stl
250.0 x 250.0 x 45.0

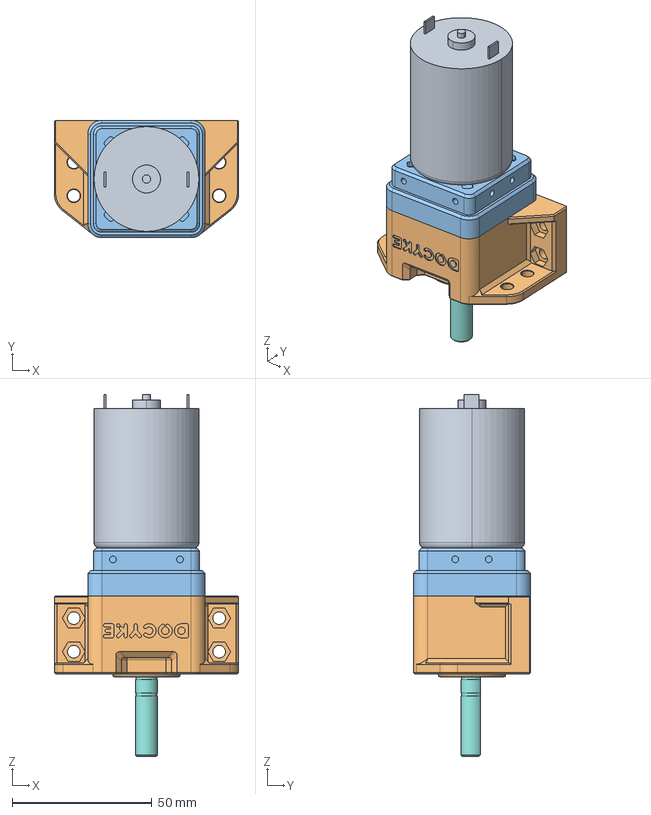
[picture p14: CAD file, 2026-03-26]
Brandan's Folder/Drive_System_Test/Hardware/model/DOCYKE DC Gear Motor.stp
66.0 x 42.0 x 129.5 mm
MOTOR_540
GEARBOX_121
GEARBOX_1
TQ
BEARING_6805
BEARING_619
SCZJ
AXIS_1

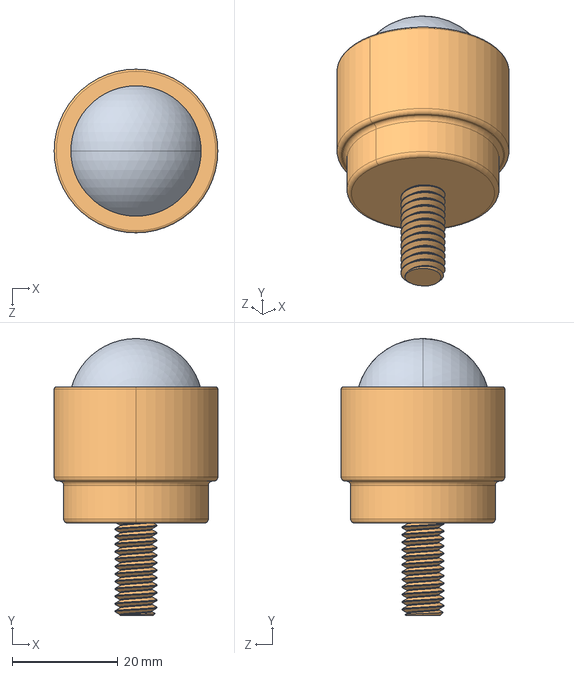
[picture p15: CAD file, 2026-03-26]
Brandan's Folder/Drive_System_Test/Hardware/Springs6460K502_Stud-Mount Ball Transfer.STEP
31.0 x 52.4 x 31.0 mm

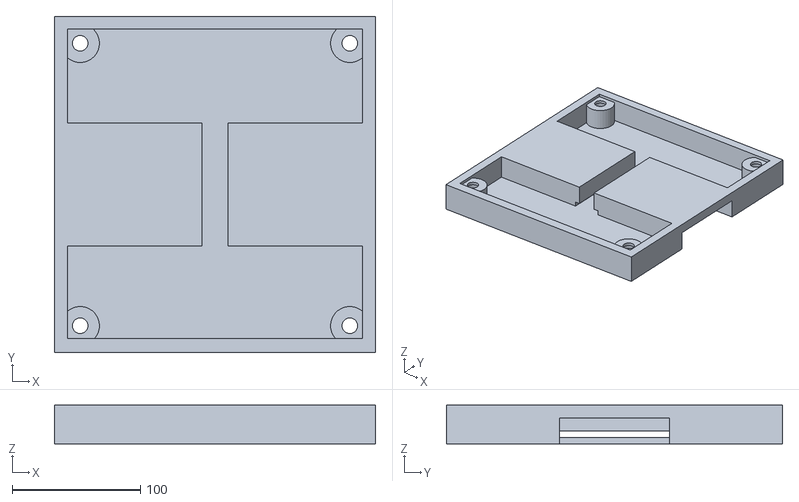
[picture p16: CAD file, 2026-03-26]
SIMULATION/Models/Parts/CyberWaster_LowerModule Platform.stl
250.0 x 262.0 x 30.0

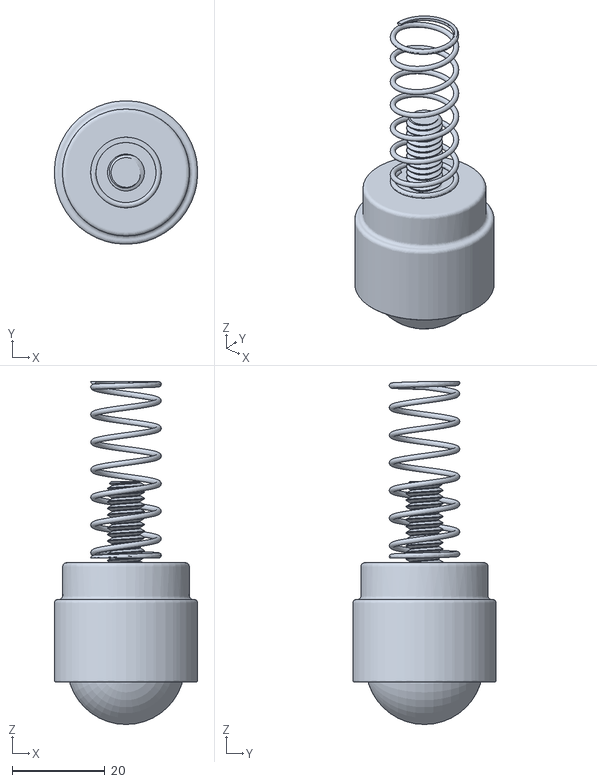
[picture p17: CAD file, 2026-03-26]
SIMULATION/Models/Sub-Assemblies/Ball Cups.stl
31.0 x 31.0 x 74.0

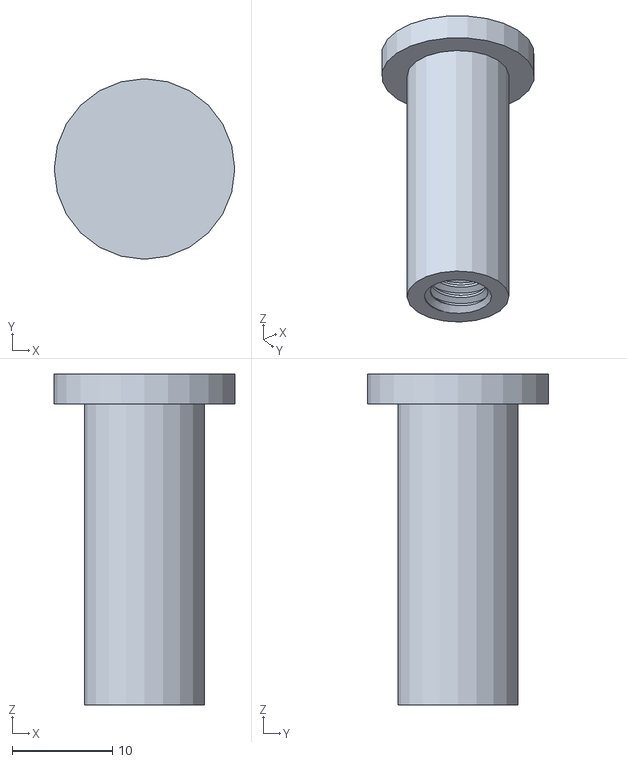
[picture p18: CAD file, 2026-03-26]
Brandan's Folder/Drive_System_Test/3DPrints/BallCup_Sring_Mount_03_07_26.stl
18.0 x 18.0 x 33.0

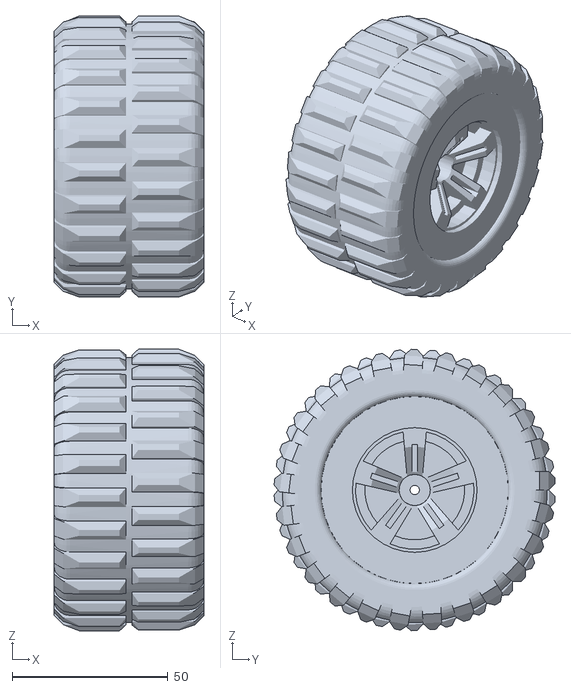
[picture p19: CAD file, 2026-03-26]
SIMULATION/Models/Parts/CyberWaster_Wheels.stl
48.0 x 90.1 x 90.3

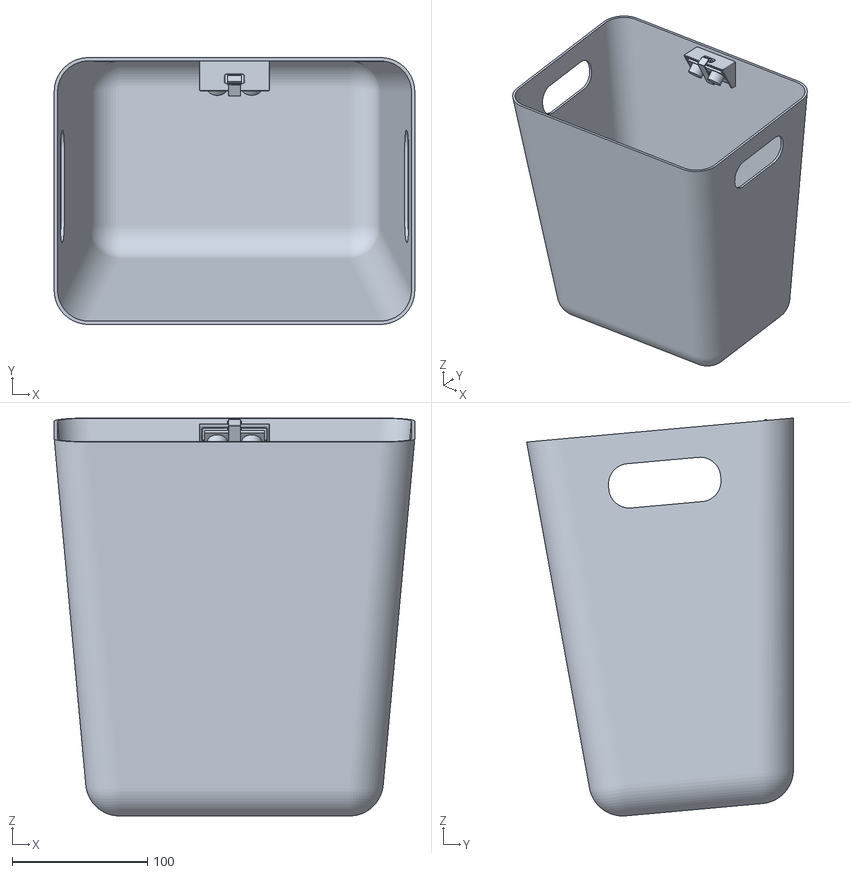
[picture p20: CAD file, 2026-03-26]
SIMULATION/Models/Sub-Assemblies/[SubMod] Housing + Bin.stl
266.7 x 197.3 x 294.3

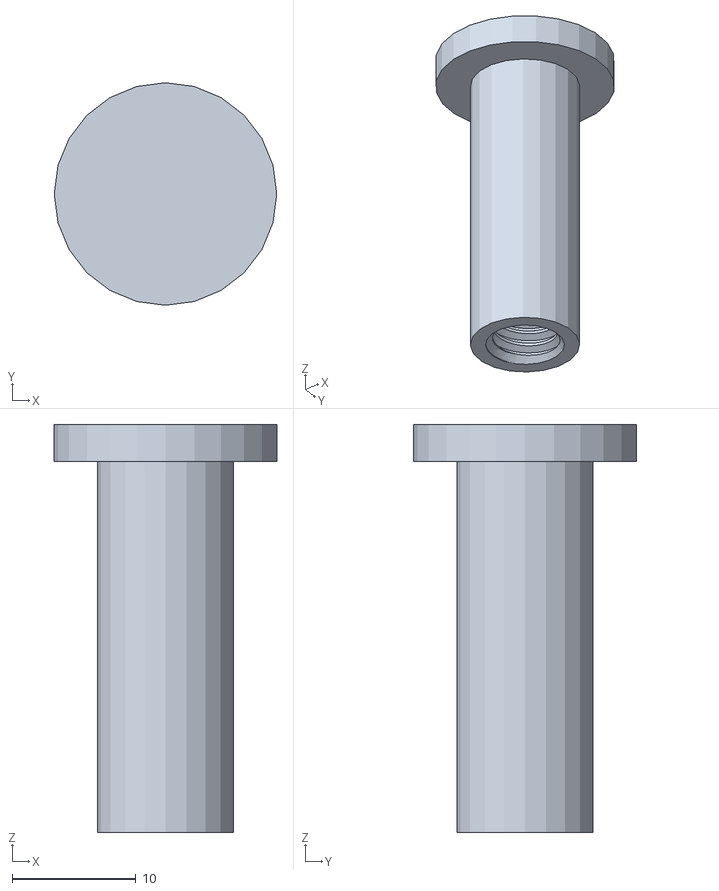
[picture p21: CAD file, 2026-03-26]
Brandan's Folder/Drive_System_Test/3DPrints/BallCup_Sring_Mount_03_07_26a.stl
18.0 x 18.0 x 33.0

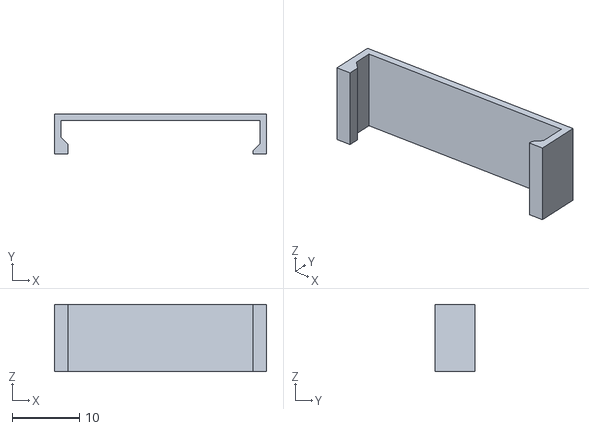
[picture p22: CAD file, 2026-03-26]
SIMULATION/Models/Parts/[Housing] Lid Snap Piece (1).stl
31.5 x 6.00 x 10.00

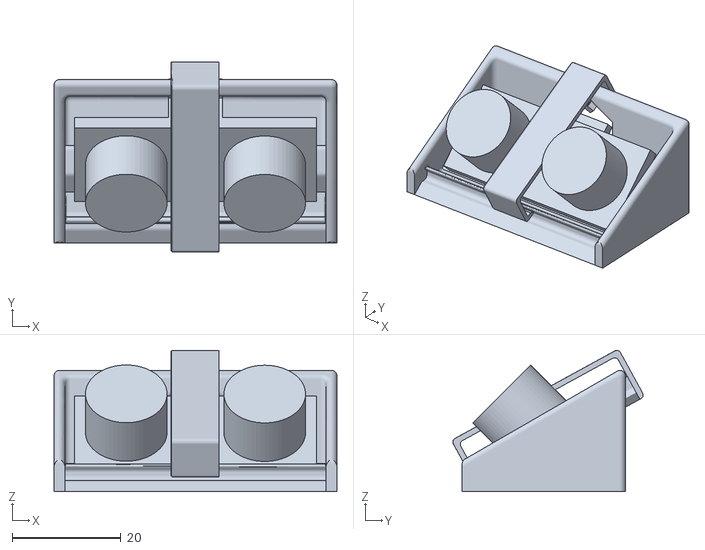
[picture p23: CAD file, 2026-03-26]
SIMULATION/Models/Sub-Assemblies/[SubMod] Ultra Sonic Alternate Option.stl
52.0 x 35.0 x 25.9

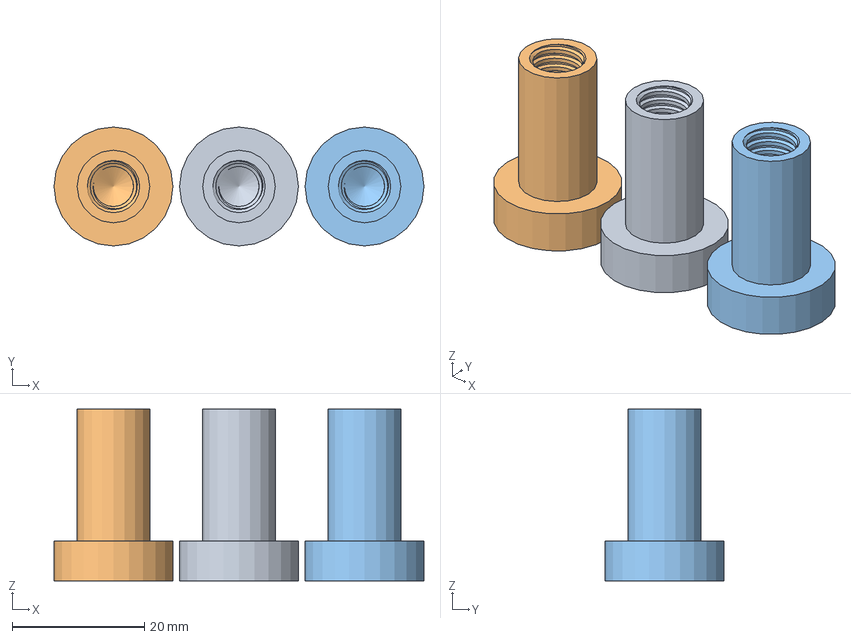
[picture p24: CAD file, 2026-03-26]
Brandan's Folder/Drive_System_Test/3DPrints/BallCup_Sring_Mount_03_09_26.3mf
56.0 x 18.0 x 26.0 mm
BallCup_Sring_Mount_03_09_26.stl x 3

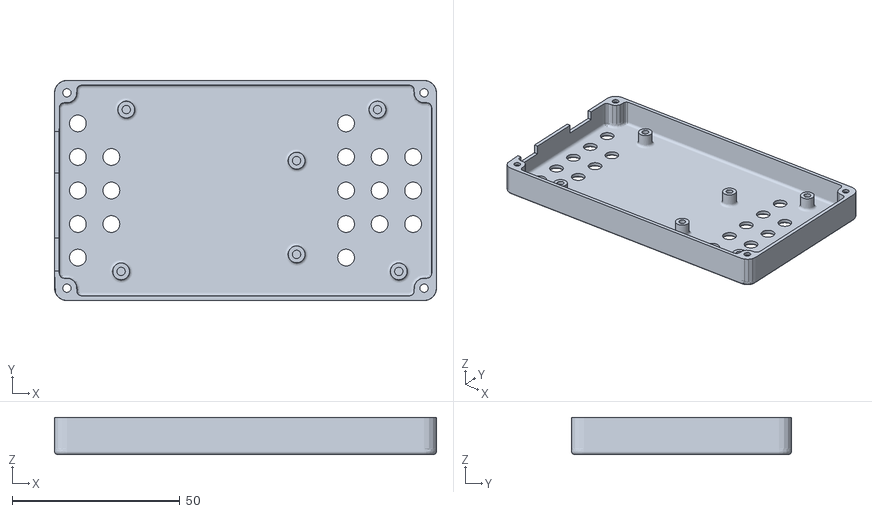
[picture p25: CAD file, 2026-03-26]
SIMULATION/Models/Parts/[Housing] Arduino Case bottom.stl
113.9 x 65.7 x 11.1

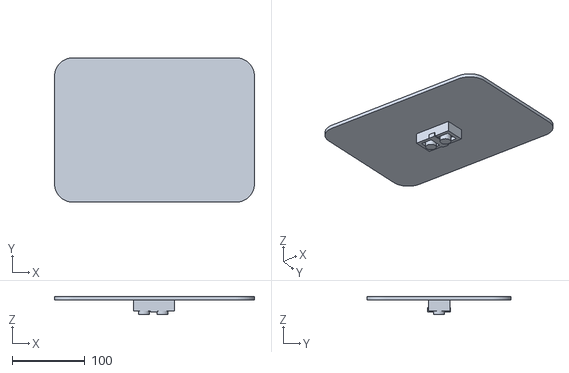
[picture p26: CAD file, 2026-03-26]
SIMULATION/Models/Sub-Assemblies/[SubMod]Lid Contraption.stl
274.3 x 198.1 x 24.7

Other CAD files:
Brandan's Folder/Drive_System_Test/Hardware/model/CyberWaster_LowerModule_03_01_26.stl
SIMULATION/Models/Parts/[Housing] Arduino Case top.stl
SIMULATION/Models/Parts/[Part] NEMA_17.stl
SIMULATION/Models/Parts/[Part] TF Luna LiDAR.stl
Brandan's Folder/Drive_System_Test/3DPrints/BallCup_Sring_Mount_03_09_26.stl
Brandan's Folder/Drive_System_Test/Hardware/Springs/9434K124_Music-Wire Steel Compression Springs.STEP
Brandan's Folder/Drive_System_Test/Hardware/Springs/9434K124_Music-Wire Steel Compression Springs_step.prt
Brandan's Folder/Drive_System_Test/Hardware/Springs/9434K74_Music-Wire Steel Compression Springs.STEP
Brandan's Folder/Drive_System_Test/Hardware/Springs/9434K74_Music-Wire Steel Compression Springs_step.prt
Brandan's Folder/Drive_System_Test/Hardware/Springs/9657K236_Compression Spring.STEP
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

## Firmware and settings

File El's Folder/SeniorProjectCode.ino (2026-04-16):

// ============================================================
//  Full System — With Kill Switch + Startup LED Test
//  Kill switch on Pin 2 (interrupt) halts all movement
// ============================================================

#include <HX711.h>

// --- STEPPER MOTOR PINS ---
#define STEP_PIN        3
#define DIR_PIN         4
#define ENABLE_PIN      5

// --- ULTRASONIC PINS ---
#define TRIG_PIN        6
#define ECHO_PIN        7

// --- HX711 PINS ---
#define HX711_DT        8
#define HX711_SCK       9

// --- LED PINS ---
#define LED_LIDAR       10  // Red
#define LED_ULTRASONIC  11  // Green
#define LED_WEIGHT      12  // Blue

// --- KILL SWITCH PIN ---
#define KILL_SWITCH_PIN 2   // Must be pin 2 or 3 for interrupt on MEGA

// --- LIDAR SERIAL ---
#define LUNA_SERIAL     Serial1
#define LUNA_BAUD       115200

// --- MOTOR SETTINGS ---
#define STEPS_PER_SWEEP 100
#define STEP_DELAY_US   800

// --- THRESHOLDS ---
#define OBSTACLE_CM     30
#define ULTRASONIC_INCH 5.0
#define WEIGHT_LBS      10.0

// --- CALIBRATION ---
#define CALIBRATION_FACTOR -7050.0

// --- GLOBALS ---
int   currentStep  = 0;
bool  sweepForward = true;
float degPerStep   = (float)180 / (float)STEPS_PER_SWEEP;
volatile bool killed = false;  // Kill switch flag — volatile because used in interrupt

HX711 scale;

// ============================================================
//  KILL SWITCH INTERRUPT
//  Triggered instantly when button is pressed
// ============================================================
void killSwitch() {
  killed = !killed;  // Toggle on/off so button can resume too
  if (killed) {
    digitalWrite(ENABLE_PIN, HIGH);   // Disable motor immediately
    digitalWrite(LED_LIDAR,      LOW);
    digitalWrite(LED_ULTRASONIC, LOW);
    digitalWrite(LED_WEIGHT,     LOW);
    Serial.println("!!! KILL SWITCH ACTIVATED — System paused !!!");
  } else {
    digitalWrite(ENABLE_PIN, LOW);    // Re-enable motor
    Serial.println("--- System resumed ---");
  }
}

// ============================================================
//  STARTUP LED SEQUENCE — Red → Green → Blue
// ============================================================
void startupLEDTest() {
  Serial.println("Running LED test...");

  // Red
  digitalWrite(LED_LIDAR, HIGH);
  delay(500);
  digitalWrite(LED_LIDAR, LOW);
  delay(200);

  // Green
  digitalWrite(LED_ULTRASONIC, HIGH);
  delay(500);
  digitalWrite(LED_ULTRASONIC, LOW);
  delay(200);

  // Blue
  digitalWrite(LED_WEIGHT, HIGH);
  delay(500);
  digitalWrite(LED_WEIGHT, LOW);
  delay(200);

  // All on together briefly as final confirmation
  digitalWrite(LED_LIDAR,      HIGH);
  digitalWrite(LED_ULTRASONIC, HIGH);
  digitalWrite(LED_WEIGHT,     HIGH);
  delay(500);
  digitalWrite(LED_LIDAR,      LOW);
  digitalWrite(LED_ULTRASONIC, LOW);
  digitalWrite(LED_WEIGHT,     LOW);

  Serial.println("LED test complete!");
  delay(300);
}

// ============================================================
//  SETUP
// ============================================================
void setup() {
  Serial.begin(115200);
  Serial.println("=== Full System Starting ===");

  // LiDAR serial
  LUNA_SERIAL.begin(LUNA_BAUD);

  // Motor pins
  pinMode(STEP_PIN,    OUTPUT);
  pinMode(DIR_PIN,     OUTPUT);
  pinMode(ENABLE_PIN,  OUTPUT);
  digitalWrite(ENABLE_PIN, LOW);
  setDirection(true);

  // Ultrasonic pins
  pinMode(TRIG_PIN, OUTPUT);
  pinMode(ECHO_PIN, INPUT);

  // LED pins
  pinMode(LED_LIDAR,       OUTPUT);
  pinMode(LED_ULTRASONIC,  OUTPUT);
  pinMode(LED_WEIGHT,      OUTPUT);

  // Kill switch — INPUT_PULLUP means no external resistor needed
  // Interrupt triggers killSwitch() instantly on button press
  pinMode(KILL_SWITCH_PIN, INPUT_PULLUP);
  attachInterrupt(
    digitalPinToInterrupt(KILL_SWITCH_PIN),
    killSwitch,
    FALLING  // Triggers when button is pressed (pin goes LOW)
  );

  // HX711 setup
  scale.begin(HX711_DT, HX711_SCK);
  scale.set_scale(CALIBRATION_FACTOR);
  scale.tare();
  Serial.println("Scale zeroed!");

  // Run startup LED test
  startupLEDTest();

  delay(500);
  Serial.println("Format: Angle, LiDAR(cm), Ultrasonic(in), Weight(lbs)");
}

// ============================================================
//  MAIN LOOP
// ============================================================
void loop() {
  // Check kill switch — if killed, do nothing until resumed
  if (killed) {
    delay(100);
    return;
  }

  // --- READ LIDAR ---
  int lidarDist = readTFLuna();
  float angle   = -90.0 + (currentStep * degPerStep);

  // --- READ ULTRASONIC ---
  float ultrasonicInch = readUltrasonic();

  // --- READ WEIGHT ---
  float weightLbs = 0;
  if (scale.is_ready()) {
    weightLbs = scale.get_units(1);
    if (weightLbs < 0) weightLbs = 0;
  }

  // --- CONTROL LEDs ---
  digitalWrite(LED_LIDAR,
    (lidarDist > 0 && lidarDist <= OBSTACLE_CM) ? HIGH : LOW);

  digitalWrite(LED_ULTRASONIC,
    (ultrasonicInch > 0 && ultrasonicInch <= ULTRASONIC_INCH) ? HIGH : LOW);

  digitalWrite(LED_WEIGHT,
    (weightLbs >= WEIGHT_LBS) ? HIGH : LOW);

  // --- PRINT STATUS ---
  Serial.print(angle, 1);
  Serial.print("°, ");
  Serial.print(lidarDist > 0 ? String(lidarDist) + "cm" : "no reading");
  Serial.print(", ");
  Serial.print(ultrasonicInch, 1);
  Serial.print("in, ");
  Serial.print(weightLbs, 2);
  Serial.println("lbs");

  // --- STEP MOTOR ---
  stepMotor();

  if (sweepForward) {
    currentStep++;
    if (currentStep >= STEPS_PER_SWEEP) {
      sweepForward = false;
      setDirection(false);
    }
  } else {
    currentStep--;
    if (currentStep <= 0) {
      sweepForward = true;
      setDirection(true);
    }
  }
}

// ============================================================
//  FUNCTION: Read TF-Luna LiDAR
// ============================================================
int readTFLuna() {
  unsigned long timeout = millis() + 50;
  while (millis() < timeout) {
    if (LUNA_SERIAL.available() >= 9) {
      if (LUNA_SERIAL.read() == 0x59) {
        if (LUNA_SERIAL.read() == 0x59) {
          byte buf[7];
          for (int i = 0; i < 7; i++) buf[i] = LUNA_SERIAL.read();
          byte checksum = 0x59 + 0x59;
          for (int i = 0; i < 6; i++) checksum += buf[i];
          if (checksum == buf[6]) return buf[0] + (buf[1] << 8);
        }
      }
    }
  }
  return 0;
}

// ============================================================
//  FUNCTION: Read HC-SR04 Ultrasonic (returns inches)
// ============================================================
float readUltrasonic() {
  digitalWrite(TRIG_PIN, LOW);
  delayMicroseconds(2);
  digitalWrite(TRIG_PIN, HIGH);
  delayMicroseconds(10);
  digitalWrite(TRIG_PIN, LOW);
  long duration = pulseIn(ECHO_PIN, HIGH, 30000);
  if (duration == 0) return -1;
  return duration * 0.0135 / 2.0;
}

// ============================================================
//  FUNCTION: Set stepper direction
// ============================================================
void setDirection(bool forward) {
  digitalWrite(DIR_PIN, forward ? HIGH : LOW);
  delayMicroseconds(200);
}

// ============================================================
//  FUNCTION: Step motor once
// ============================================================
void stepMotor() {
  digitalWrite(STEP_PIN, HIGH);
  delayMicroseconds(STEP_DELAY_US);
  digitalWrite(STEP_PIN, LOW);
  delayMicroseconds(STEP_DELAY_US);
}

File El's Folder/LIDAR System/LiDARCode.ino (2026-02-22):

// PIN Definitons
#define STEP_PIN 3   // A4988 pin
#define DIR_PIN 4   // A4988 pin
#define ENABLE_PIN 5   // A4988 ENABLE pin (LOW = enabled)

//     Sweep Functionality:
// Sweep ±90° front facing
#define STEPS_PER_REV 200
#define STEP_DELAY_US 1500 // Adjust as needed
#define SWEEP_DEGREES 180
#define STEPS_PER_SWEEP     (STEPS_PER_REV * SWEEP_DEGREES / 360) // should make about 100 distinct steps, more than enough. (Adjust as needed)

// Define distance at which an obstacle is an obstacle
#define OBSTACLE_DISTANCE_CM  50 //Adjust as needed

// Set up serial session with the LiDAR
#define LUNA_SERIAL   Serial1
#define LUNA_BAUD     115200

// Variable definitons
int currentSweep = 0;
bool sweepForward = True;
float degPerStep = SWEEP_DEGREES/STEPS_PER_SWEEP

void setup() {
  //Output Data to PC (testing):
  Serial.begin(115200);
  Serial.println("=== LiDAR Sweep Scanner Starting ===");
  Serial.println("Format: Angle(deg), Distance(cm), Status");
  
  // Start TF-Luna serial
  LUNA_SERIAL.begin(LUNA_BAUD);
  pinMode(STEP_PIN,   OUTPUT);
  pinMode(DIR_PIN,    OUTPUT);
  pinMode(ENABLE_PIN, OUTPUT);

  digitalWrite(ENABLE_PIN, LOW);

  //Choose starting sweep direction, True = positive direction first
  setDirection(true);

  delay(500);
}

// main but c++
void loop(){ 
  //read distance from the TF luna LiDAR
  int distance = readTFLuna();

  //variable to contain current angle
  float angle = -90.0 + (currentStep * degPerStep);

  // [Insert data output here]
  
  //Move one step
  stepMotor();

  // Update sweep step and direction if needed.
  if (sweepForward) {
    currentStep++;
    if (currentStep >= STEPS_PER_SWEEP) {
      sweepForward = false;
      setDirection(false);        // Reverse direction
    }
  } else {
    currentStep--;
    if (currentStep <= 0) {
      sweepForward = true;
      setDirection(true);         // Forward direction
    }
  }
}

// forward = true -> sweep left to right, forward = false -> right to left
// May want to make this an input that can be adjusted in real time to change direction to direction of movement
void setDirection(bool forward) {
  digitalWrite(DIR_PIN, forward ? HIGH : LOW);
  delayMicroseconds(5); // Small delay after changing direction (required by A4988)
}

// move the motor 1 step for the scan
void stepMotor() {
  digitalWrite(STEP_PIN, HIGH);
  delayMicroseconds(STEP_DELAY_US);
  digitalWrite(STEP_PIN, LOW);
  delayMicroseconds(STEP_DELAY_US);
}

//read the distance from the LiDAR
int readTFLuna() {
  // Timeout after ~50ms
  unsigned long timeout = millis() + 50;
  while (millis() < timeout) {
    if (LUNA_SERIAL.available() >= 9) {
      // Look for the two-byte header: 0x59 0x59
      if (LUNA_SERIAL.read() == 0x59) {
        if (LUNA_SERIAL.read() == 0x59) {
          // Read the remaining 7 bytes
          byte buf[7];
          for (int i = 0; i < 7; i++) {
            buf[i] = LUNA_SERIAL.read();
          }

          // buf[0] = distance low byte
          // buf[1] = distance high byte
          int dist = buf[0] + (buf[1] << 8);  // Combine into 16-bit int

          // Checksum = lower 8 bits of sum of all bytes 0x59+0x59+buf[0..5]
          // helps counter invalid data inputs
          byte checksum = 0x59 + 0x59;
          for (int i = 0; i < 6; i++) {
            checksum += buf[i];
          }
          // buf[6] is the checksum byte from the sensor
          if (checksum == buf[6]) {
            return dist;  // Valid reading in cm
          }
          // Checksum failed - flush and try again
        }
      }
    }
  }

  return 0; // in case of time out or bad reading
}

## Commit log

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2026-03-15 Simulation World 1 March 15 (Before Slope)
    This is the Simulation world of the home area/driveway.
    [project_map1.sdf]
2026-03-15 Update project_map1.sdf March 15 (Commented)
    Commented out placeholder robot.
    [project_map1.sdf]
2026-03-15 Rename SIMULATION/project_map1.sdf to SIMULATION/Worlds/project_map1.sdf
    Creating Folder called Worlds in SIMULATION folder to place all worlds inside.
    [project_map1.sdf]
2026-03-15 Simulation_World2 March 15 (Warehouse)
    Added the warehouse environment for Gazebo
    [project_map2.sdf]
2026-03-15 Simulation_World3 March 15 (Senior Homecare)
    Added the Senior Homecare environment for Gazebo.
    [project_map3.sdf]
2026-03-15 Update project_map2.sdf (Commented)
    Commented out the placeholder robot.
    [project_map2.sdf]
2026-03-15 Update project_map3.sdf (Commented)
    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
    [project_map3.sdf]
2026-03-26 Rename SIMULATION/Models/Full Assembly (1)(1).stl to SIMULATION/Models/Full Model/Full Assembly.stl
    [Full Assembly.stl]
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2026-03-26 Rename Brednan's Folder/Drive_System_Test/3DPrints/BallCup_Sring_Mount_03_07_26.stl to Brandan's Folder/Drive_System_Test/Drive_System_Test 3DPrints BallCup_Sring_Mount_03_07_26.stl
    [Drive_System_Test 3DPrints BallCup_Sring_Mount_03_07_26.stl]
2026-03-26 Rename Brandan's Folder/Drive_System_Test/Drive_System_Test 3DPrints BallCup_Sring_Mount_03_07_26.stl to Brandan's Folder/Drive_System_Test/3DPrints/BallCup_Sring_Mount_03_07_26.stl
    [BallCup_Sring_Mount_03_07_26.stl]
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2026-03-26 Rename DOCYKE DC Gear Motor.stp to DOCYKE DC Gear Motor.stp
    [DOCYKE DC Gear Motor.stp]
2026-03-26 Rename 9434K124_Music-Wire Steel Compression Springs.STEP to 9434K124_Music-Wire Steel Compression Springs.STEP
    [9434K124_Music-Wire Steel Compression Springs.STEP]
2026-03-26 Rename 9434K124_Music-Wire Steel Compression Springs_step.prt to 9434K124_Music-Wire Steel Compression Springs_step.prt
    [9434K124_Music-Wire Steel Compression Springs_step.prt]
2026-03-26 Rename 9434K74_Music-Wire Steel Compression Springs.STEP to 9434K74_Music-Wire Steel Compression Springs.STEP
    [9434K74_Music-Wire Steel Compression Springs.STEP]
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2026-03-26 Rename 9434K74_Music-Wire Steel Compression Springs_step.prt to 9434K74_Music-Wire Steel Compression Springs_step.prt
    [9434K74_Music-Wire Steel Compression Springs_step.prt]
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2026-03-26 Rename Brednan's Folder/Drive_System_Test/Hardware/ball/6460K502_Stud-Mount Ball Transfer.STEP to Brandan's Folder/Drive_System_Test/Hardware/Springs6460K502_Stud-Mount Ball Transfer.STEP
    [Springs6460K502_Stud-Mount Ball Transfer.STEP]
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2026-03-26 Rename 6460K502_Stud-Mount Ball Transfer_step.prt to 6460K502_Stud-Mount Ball Transfer_step.prt
    [6460K502_Stud-Mount Ball Transfer_step.prt]
2026-03-26 Rename 6460K538_Stud-Mount Ball Transfer.STEP to 6460K538_Stud-Mount Ball Transfer.STEP
    [6460K538_Stud-Mount Ball Transfer.STEP]
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2026-03-26 Rename 6460K538_Stud-Mount Ball Transfer_step.prt to 6460K538_Stud-Mount Ball Transfer_step.prt
    [6460K538_Stud-Mount Ball Transfer_step.prt]
2026-03-26 Rename 6460K551_Stud-Mount Ball Transfer.SLDPRT to 6460K551_Stud-Mount Ball Transfer.SLDPRT
    [6460K551_Stud-Mount Ball Transfer.SLDPRT]
2026-03-26 Rename 6460K551_Stud-Mount Ball Transfer.STEP to 6460K551_Stud-Mount Ball Transfer.STEP
    [6460K551_Stud-Mount Ball Transfer.STEP]
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2026-03-26 Rename 6460K551_Stud-Mount Ball Transfer_step.prt to 6460K551_Stud-Mount Ball Transfer_step.prt
    [6460K551_Stud-Mount Ball Transfer_step.prt]
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2026-03-26 Rename Wheel 85 mm.step to Wheel 85 mm.step
    [Wheel 85 mm.step]
2026-03-26 Rename Wheel 85 mm.stl to Wheel 85 mm.stl
    [Wheel 85 mm.stl]
2026-03-26 Rename Wheel 85 mm_step.prt to Wheel 85 mm_step.prt
    [Wheel 85 mm_step.prt]
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2026-03-26 Rename Brednan's Folder/Drive_System_Test/Model/Ardunio Mega _1_.prt to Brandan's Folder/Drive_System_Test/Hardware/model/Ardunio Mega _1_.prt
    [Ardunio Mega _1_.prt]
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2026-03-26 Rename 6460K538_Stud-Mount Ball Transfer.SLDPRT to 6460K538_Stud-Mount Ball Transfer.SLDPRT
    [6460K538_Stud-Mount Ball Transfer.SLDPRT]
2026-03-26 Rename 4329N11_Swivel T-Slotted Framing Caster.SLDPRT to 4329N11_Swivel T-Slotted Framing Caster.SLDPRT
    [4329N11_Swivel T-Slotted Framing Caster.SLDPRT]
2026-03-26 Rename 4329N11_Swivel T-Slotted Framing Caster.STEP to 4329N11_Swivel T-Slotted Framing Caster.STEP
    [4329N11_Swivel T-Slotted Framing Caster.STEP]
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2026-03-26 Rename Brednan's Folder/Drive_System_Test/Model/DOCYKE DC Gear Motor.stp to Brandan's Folder/Drive_System_Test/Hardware/model/DOCYKE DC Gear Motor.stp
    [DOCYKE DC Gear Motor.stp]
2026-03-26 Rename Brednan's Folder/Drive_System_Test/Model/DOCYKE DC Gear Motor_stp.prt to Brandan's Folder/Drive_System_Test/Hardware/model/DOCYKE DC Gear Motor_stp.prt
    [DOCYKE DC Gear Motor_stp.prt]
2026-04-07 Update project_map1.sdf April 7 (Slope Floor)
    I forgot to add the update to map 1 that it now has a slope.
    [project_map1.sdf]
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
